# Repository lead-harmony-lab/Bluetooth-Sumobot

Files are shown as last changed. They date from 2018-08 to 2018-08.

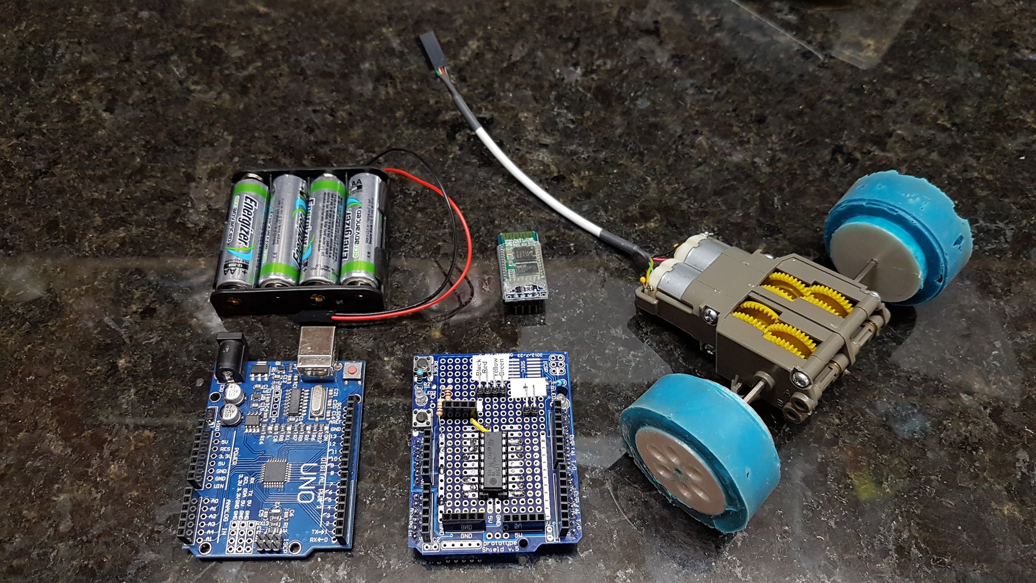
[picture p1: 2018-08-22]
20180820_223847.jpg

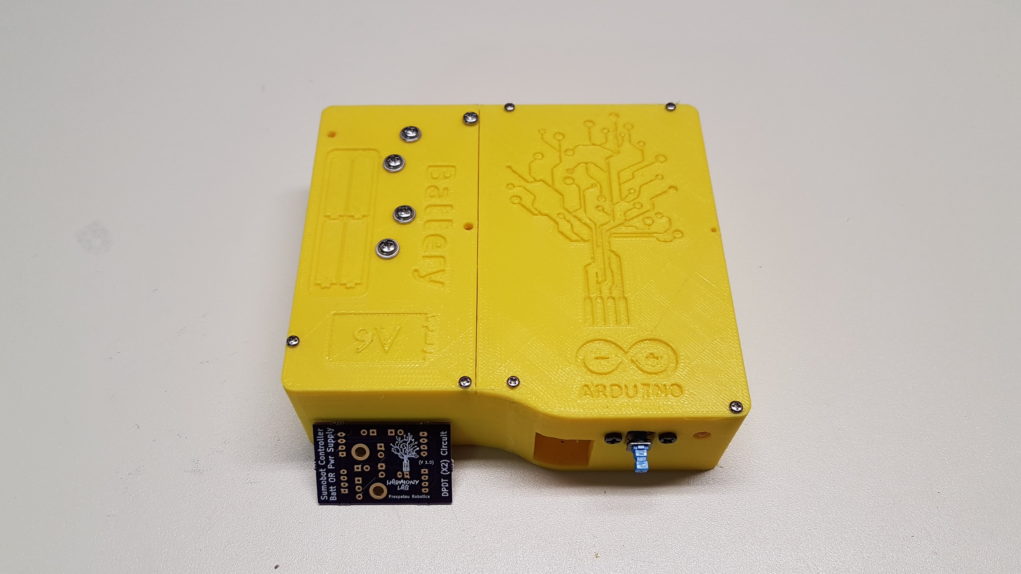
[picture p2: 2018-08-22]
20180819_121456.jpg

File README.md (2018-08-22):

# Bluetooth-Sumobot
Processing code and STL files for the BlueTooth controlled sumobot based on the HC06 module

# Controlling the Sumobot
Download and side-load the [Android app (Arduino Bluetooth Controller)](https://github.com/lead-harmony-lab/Bluetooth-Sumobot/blob/master/Arduino%20bluetooth%20controller_v1.3_apkpure.com.apk) (APK file tested in Android 8.0 on a Samsung S7) - August 2018. 
After installing the app and confirming that your BlueTooth is turned on:
1. Pair with the HC06 module (may be named HC06)
2. Enter password to pair with module (default may be '1234')
3. Launch app.
4. Select module (HC06) from the list of available devices. If not available, confirm step 1.
5. The app will ask which mode to select. Choose 'Controller mode' from top of the list.
6. Confirm solid light on the HC06 module indicating pairing was successful
7. Choose gear/settings icon from top right corner.
8. Configure the field for each icon using these strings. The icon shape is described in the [ ] braces. See [this image](https://github.com/lead-harmony-lab/Bluetooth-Sumobot/blob/master/Arduino%20bluetooth%20controller%20setup%20image.jpg) for a visual guide.
                
                [left arrow] left
                [up arrow] forward
                [right arrow] right
                [down arrow] reverse
                
                [select]
                [start]

                [square] half
                [triangle] faster
                [X] stop
                [circle] slower
REMEMBER: You must select done / checkmark on the keyboard to lock the changes into the app. Otherwise the app will continue to show 'not set' after you have entered in the appropriate text. 

9. Return to the previous screen using the Android back button.
10. Control the sumobot by pressing on the control icons.

# Customizing the Android App
The code for [a basic Android Studio project](https://github.com/lead-harmony-lab/Bluetooth-Sumobot/tree/master/Android%20Sumobot%20Controller/app/src/main) can be modified to add any additional behaviour to the controller that you require. Simply create an new 'Empty Activity' when creating a new project. When the project is loaded, copy over the basic project files into your new project's directory. **REMEMBER** to look up the MAC address of your Bluetooth module and replace the DEVICE ADDRESS in MainActivity.java in order to get this app to work with your Bluetooth module.

# Building the control board
The schematic for controlling this sumbot has been created in KiCad. The gerber files can be sent to a board house (I use [OSHPark](https://oshpark.com)) for fabrication. The schematic can also be used as a basis for putting together a breadboarded version of this project. I've included a hand-drawn image of the pinout I used for the L293D IC when connecting to the Arduino Uno.

# Model File
All of the 3D design work was done in Blender using millimeters. I used Blender 2.79b on Ubuntu 18.04 Linux.

# 3D Printing
I printed these parts out on an FDM RepRap based printer - The Robo3D R1+. Total print time is approximately 24 hours. I recommend that you print the sumobot body on its roof with the motor cavity facing up towards the nozzle. I have found that this model will print successfully without the need to also add support material. I use Matter Control software to control the 3D Printer.

# Arduino Processing Program
Code for this project is complied from a variety of sources from around the Internet. A big shout-out to all the generous people out there that share their code and who make tutorials for other people to follow. I used the Arduino IDE 1.8.5.

# Parts
* Sumobot
  * Tamiya Twin-Motor Gearbox 70097
  * 4-strand data cable
  * Silicon (OooGoo) wheel grips (you will have to design your own hubs)
* BlueTooth Module
  * HC06 Bluetooth Module https://www.ebay.ca/itm/201415076859
  * Single battery (pos & neg) terminals: https://www.ebay.ca/itm/311070764299
  * Battery conversion spring: https://www.ebay.ca/itm/172440758009
  * Latching DPDT switch: https://www.ebay.ca/itm/322498646783
  * Single-row male header pins: https://www.ebay.ca/itm/181918556293
  * Single-row female header socket: https://www.ebay.ca/itm/192600775159
  * 1K axial resistor
  * 2K axial resistor
  * 150R axial resistor
  * 100uf electrolytic capacitor: https://www.ebay.ca/itm/291535579746
  * 0.1uf ceramic capacitor: https://www.ebay.ca/itm/323377133385
  * L293D IC (Quadruple H-Bridge driver with internal fly-back diodes): https://www.ebay.ca/itm/311173671055
  * 16 pin DIP socket: https://www.ebay.ca/itm/311563518356
  * Arduino UNO: https://www.ebay.ca/itm/263452480977
  * Arduino UNO prototype shield: https://www.ebay.ca/itm/172536470483
  * 4 AA Batteries
  * 9V Battery
  * 9 Volt Battery Clip: https://www.ebay.ca/itm/263766384151
  * Hook-up wire: https://www.ebay.ca/itm/372234345012
  * Heat Shrink Tubing: https://www.ebay.ca/itm/381381208587
  * Dupont 4-Pin 2.54mm Housing: https://www.ebay.ca/itm/152837501538
  * Dupont 2-Pin 2.54mm Housing: https://www.ebay.ca/itm/331824268796
  * Dupont Female Connector Terminal: https://www.ebay.ca/itm/141975933772
  * HT-225D Dupont Crimping Tool: https://www.ebay.ca/itm/263766640490
  * M2 x 8mm self-tapping screws: https://www.ebay.ca/itm/182309825046?var=484855861567
  * M3 x 6mm self-tapping screws: https://www.ebay.ca/itm/182309825046?var=484855861608

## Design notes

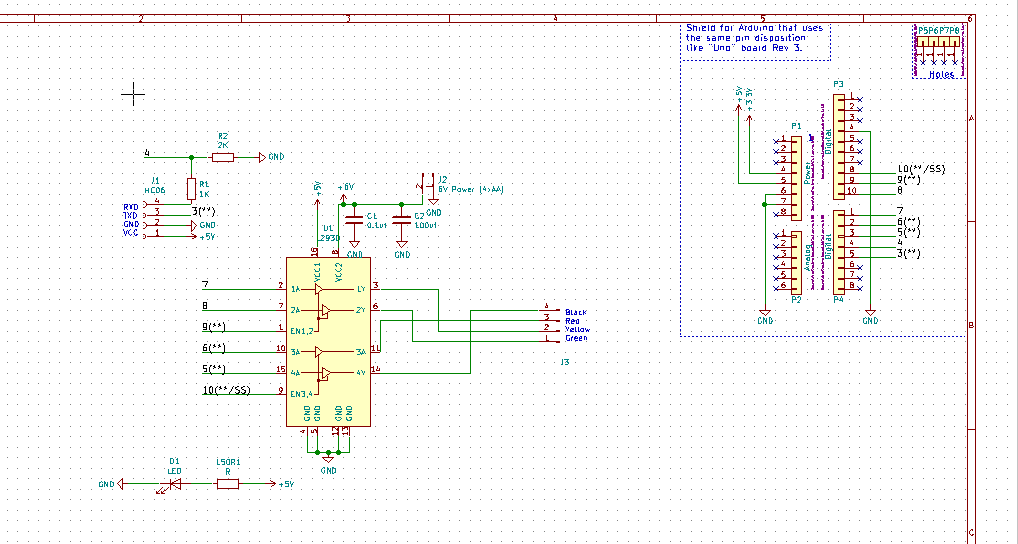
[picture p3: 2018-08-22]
Schematic.png

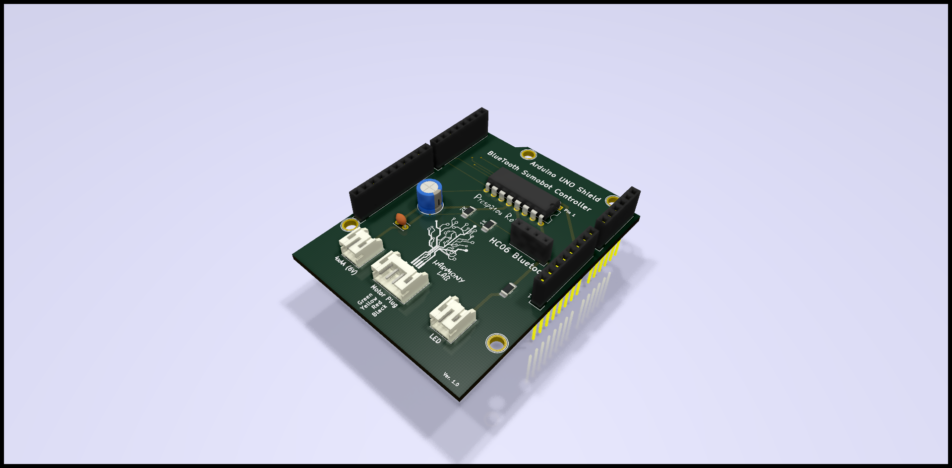
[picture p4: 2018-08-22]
L293D BlueTooth UNO Shield/Bluetooth Sumobot UNO Shield V1 Profile.png

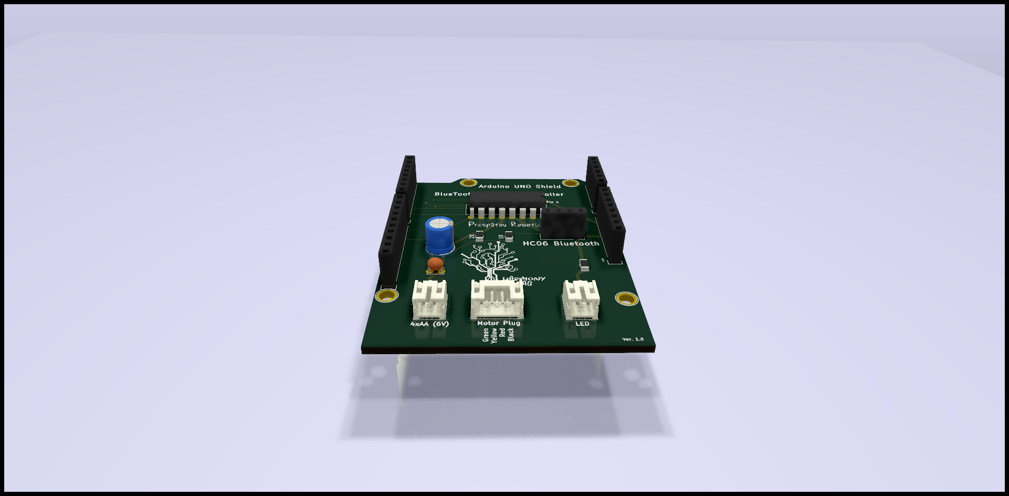
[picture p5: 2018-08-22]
L293D BlueTooth UNO Shield/Bluetooth Sumobot UNO Shield V1 Front.png

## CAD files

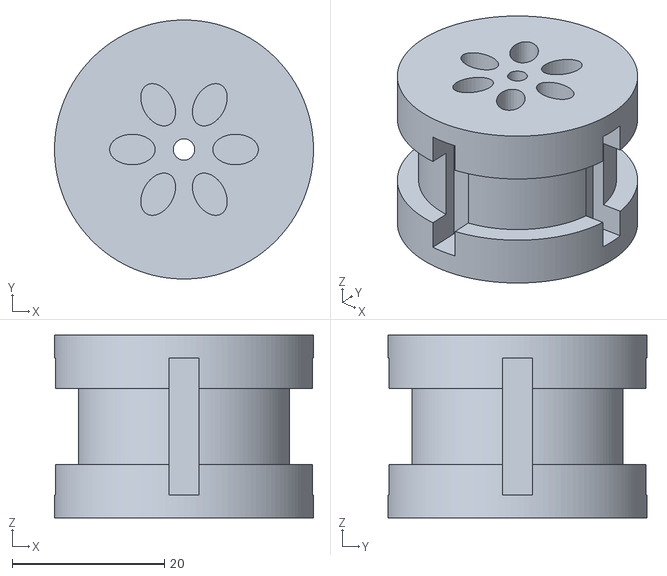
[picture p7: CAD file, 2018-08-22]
3D Model (Blender & STL)/Wheel Hub.stl
34.0 x 34.0 x 24.0

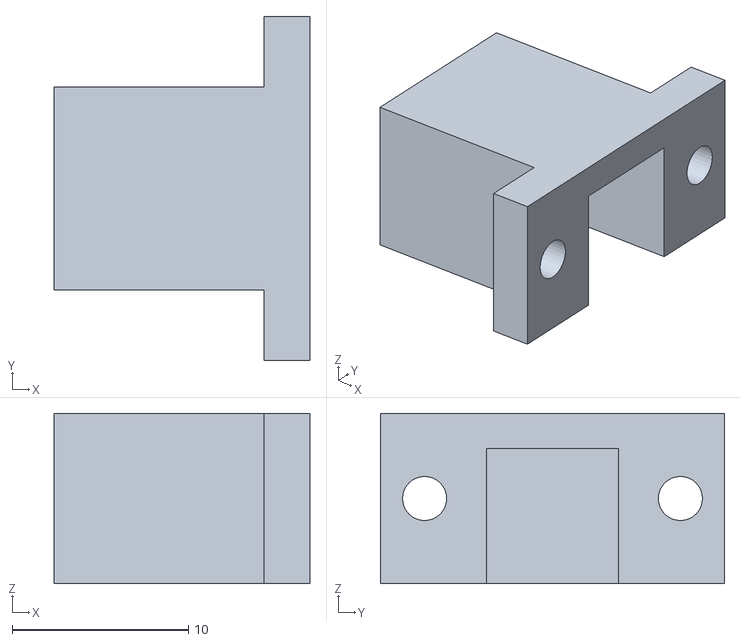
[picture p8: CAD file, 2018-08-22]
3D Model (Blender & STL)/Switch Mount.stl
14.5 x 19.5 x 9.65

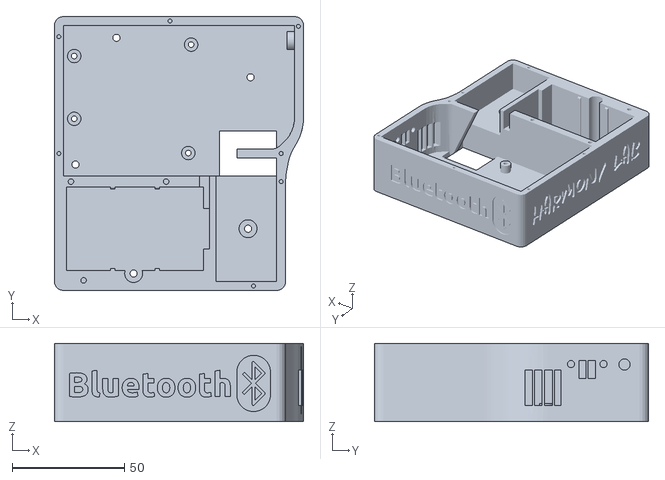
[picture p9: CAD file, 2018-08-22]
3D Model (Blender & STL)/Project Box.stl
111.0 x 122.0 x 34.9

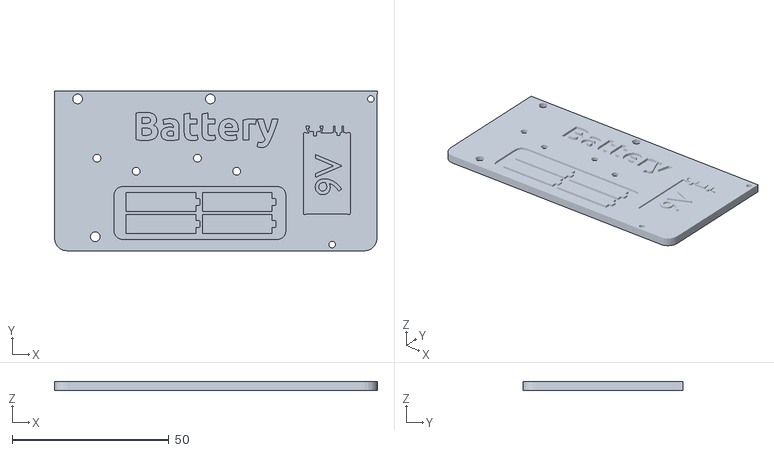
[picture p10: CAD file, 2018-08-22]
3D Model (Blender & STL)/Lid 2.stl
103.1 x 51.0 x 3.00

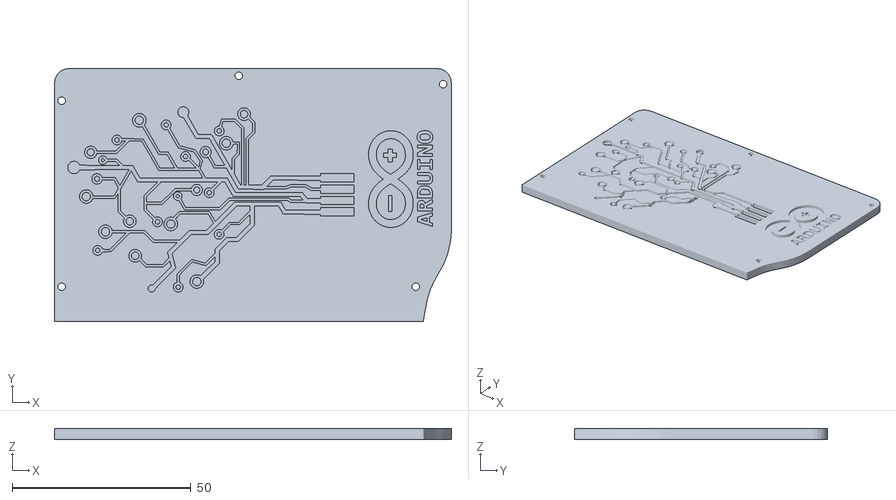
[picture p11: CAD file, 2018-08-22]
3D Model (Blender & STL)/Lid 1.stl
111.0 x 70.7 x 3.00

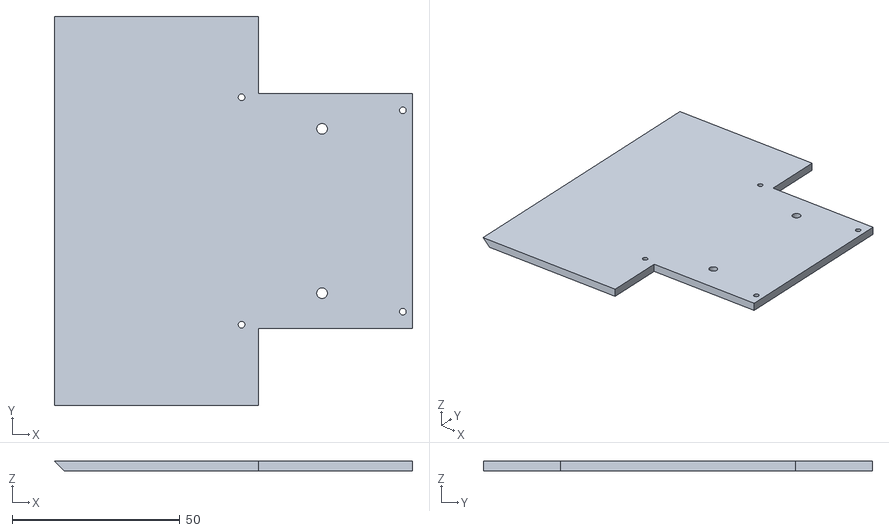
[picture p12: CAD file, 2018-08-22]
3D Model (Blender & STL)/Sumobot Motor Mounting Plate.stl
106.8 x 116.0 x 3.00

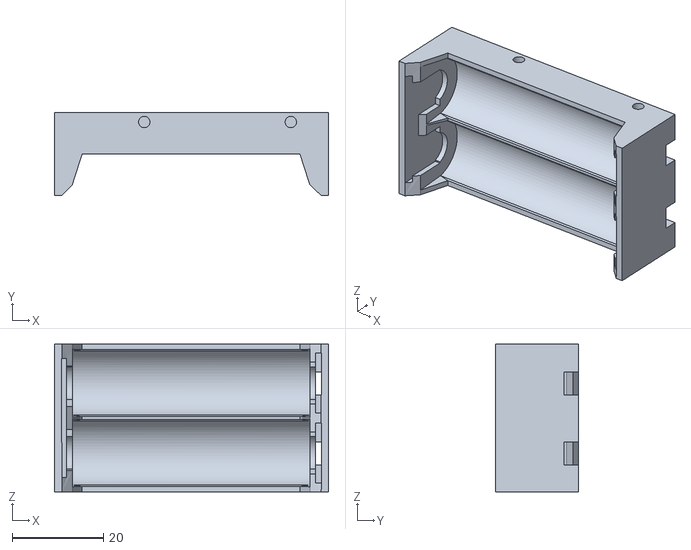
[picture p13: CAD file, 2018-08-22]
3D Model (Blender & STL)/Battery Box.stl
60.0 x 18.2 x 32.4

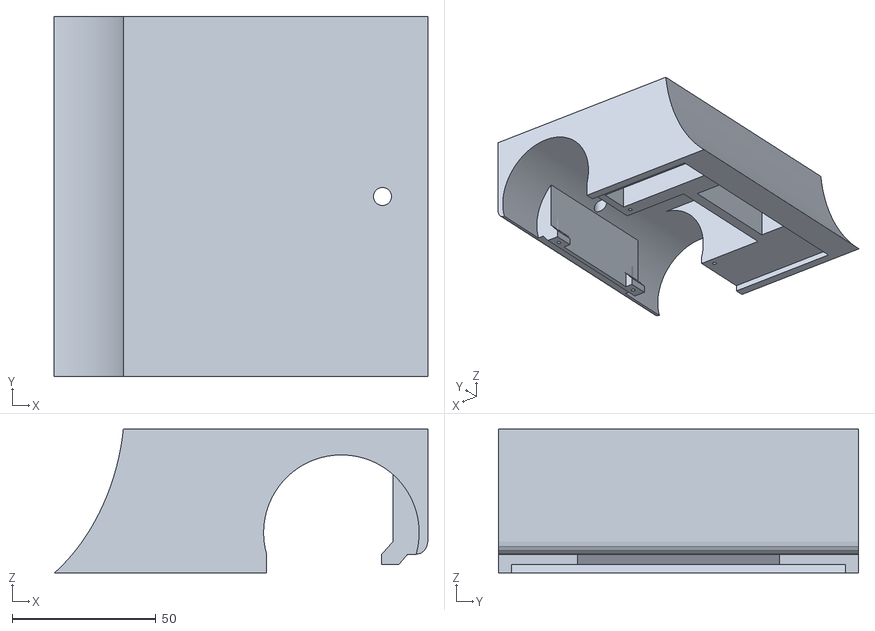
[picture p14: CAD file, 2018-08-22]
3D Model (Blender & STL)/Sumobot Body.stl
129.7 x 125.0 x 50.0

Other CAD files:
3D Model (Blender & STL)/Wheel Hub.blend

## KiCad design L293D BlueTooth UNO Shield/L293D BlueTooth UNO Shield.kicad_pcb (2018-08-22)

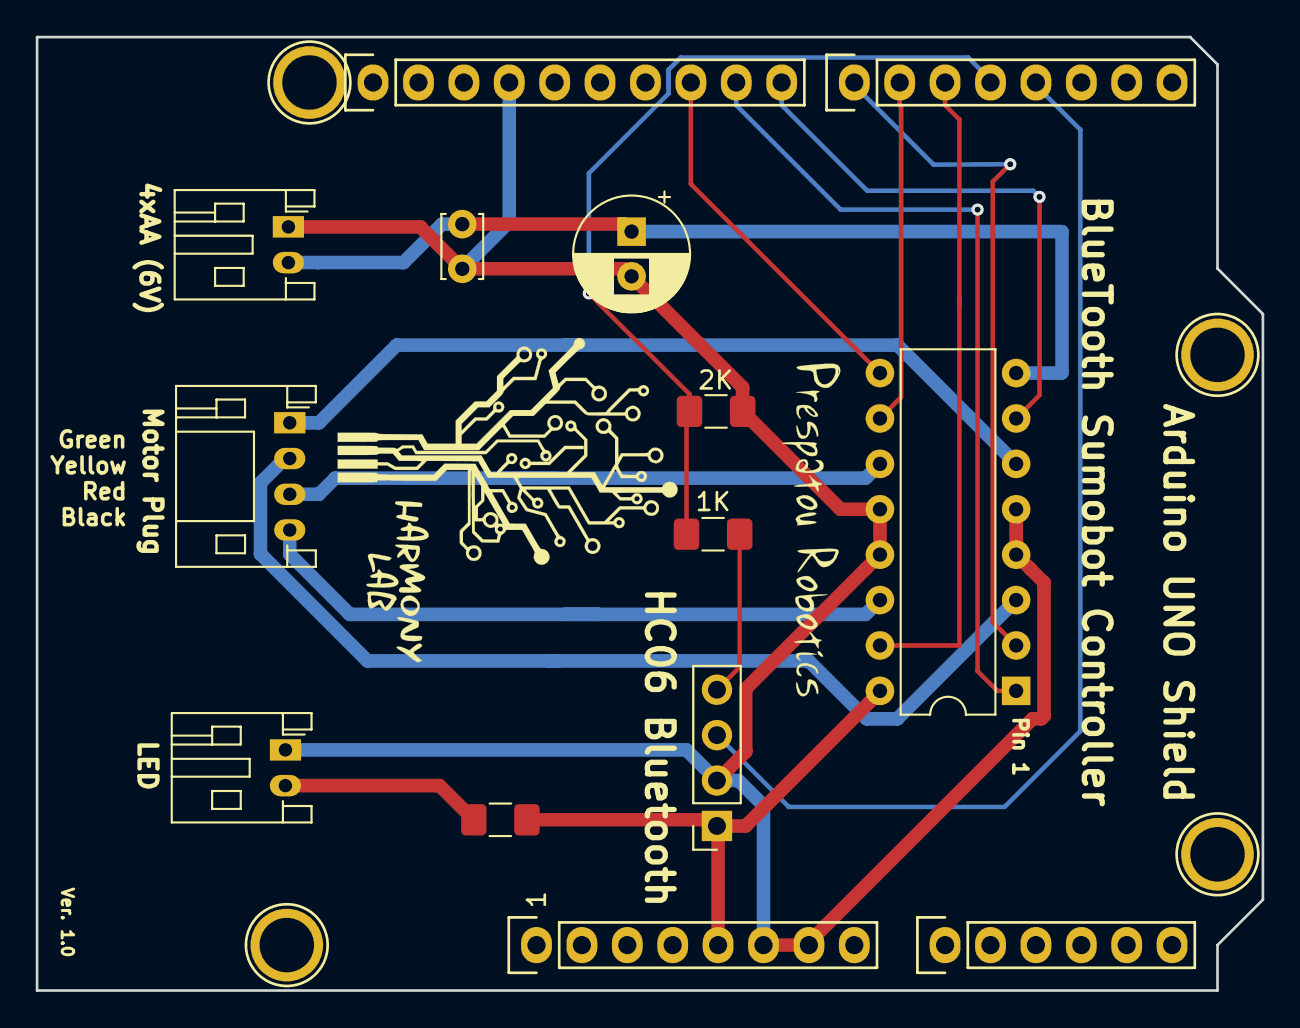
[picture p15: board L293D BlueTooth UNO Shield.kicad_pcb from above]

Board: 2 copper layers, 68.6 x 53.3 mm, 18 parts (0 on the bottom side), 17 nets.

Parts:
1K: 1K; R_1206_3216Metric_Pad1.42x1.75mm_HandSolder
2K: 2K; R_1206_3216Metric_Pad1.42x1.75mm_HandSolder
150R1: R; R_1206_3216Metric_Pad1.42x1.75mm_HandSolder
C1: 0.1uf; C_Disc_D3.4mm_W2.1mm_P2.50mm
C2: 100uf; CP_Radial_D6.3mm_P2.50mm
D1: LED; JST_PH_S2B-PH-K_1x02_P2.00mm_Horizontal
J1: HC06; PinSocket_1x04_P2.54mm_Vertical
J2: 6V Power (4xAA); JST_PH_S2B-PH-K_1x02_P2.00mm_Horizontal
J3: Motor Connector; JST_PH_S4B-PH-K_1x04_P2.00mm_Horizontal
P1: Power; Socket_Strip_Arduino_1x08
P2: Analog; Socket_Strip_Arduino_1x06
P3: Digital; Socket_Strip_Arduino_1x10
P4: Digital; Socket_Strip_Arduino_1x08
P5, P6, P7, P8: CONN_01X01; Arduino_1pin
U1: L293D; DIP-16_W7.62mm

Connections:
+5V: 150R1.1, J1.1, P1.5, U1.16
+6V: C1.1, C2.1, J2.2, U1.8
/3(**): J1.3, P4.5
/4: 1K.1, 2K.2, P4.4
/5(**): P4.3, U1.15
/6(**): P4.2, U1.10
/7: P4.1, U1.2
/8: P3.10, U1.7
/9(**): P3.9, U1.1
/10(**/SS): P3.8, U1.9
GND: 2K.1, C1.2, C2.2, D1.1, J1.2, J2.1, P1.6, P1.7, P3.4, U1.4, U1.5, U1.12, U1.13
unnamed: 150R1.2, D1.2
unnamed: 1K.2, J1.4
unnamed: J3.1, U1.6
unnamed: J3.2, U1.3
unnamed: J3.3, U1.11
unnamed: J3.4, U1.14

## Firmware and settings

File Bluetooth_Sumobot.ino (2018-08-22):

#include <SoftwareSerial.h>
SoftwareSerial BlueTooth(3, 4); // (RX, TX) - These are the pins on the Arduino we are using instead of the built-in RX and TX pins
// Connect the HC-06 TX to the Arduino RX on pin 3. 
// Connect the HC-06 RX to the Arduino TX on pin 4 through a voltage divider.

//L293D
//Motor A
const int motorPin1  = 5;   // Pin 14 of L293D
const int motorPin2  = 6;   // Pin 10 of L293D
//Motor B
const int motorPin3  = 8;   // Pin  7 of L293D
const int motorPin4  = 7;   // Pin  2 of L293D
//Enable Motors
const int enableLeftMotorSwitch = 9;   // Pin  1 of L293D
const int enableRightMotorSwitch = 10;  // Pin  9 of L293D

String msg;
char c;
int motorSpeed = 255; // Motor speed is an number between 0 - 255. Half speed is 153.

//This will run only one time.
void setup(){
  
  // HC-06 default serial speed is 9600
  BlueTooth.begin(9600); 
  Serial.begin(9600);

  //Motor Control - Motor A: motorPin1,motorpin2 & Motor B: motorpin3,motorpin4
  //Set pins as outputs
  pinMode(motorPin1, OUTPUT);
  pinMode(motorPin2, OUTPUT);
  pinMode(motorPin3, OUTPUT);
  pinMode(motorPin4, OUTPUT);

  pinMode(enableLeftMotorSwitch, OUTPUT);
  pinMode(enableRightMotorSwitch, OUTPUT);

}


void loop(){
  msg = "";

  analogWrite(enableLeftMotorSwitch, motorSpeed);
  analogWrite(enableRightMotorSwitch, motorSpeed);
  
  while(BlueTooth.available()){
    c = BlueTooth.read();
    msg += String(c);
    delay(5);
  }

  if(msg == "forward"){
    rightMotorForward();
    leftMotorForward();
  }
  else if(msg == "reverse"){
    rightMotorReverse();
    leftMotorReverse();
  }
  else if(msg == "right"){
    rightMotorStop();
    leftMotorForward();
  }
  else if(msg == "left"){
    rightMotorForward();
    leftMotorStop();
  }
  else if(msg == "half"){
    halfSpeed();
  }
  else if(msg == "stop"){
    stoprobot();
  }
  else if(msg == "faster"){
    increaseSpeed();
  }
  else if(msg == "slower"){
    decreaseSpeed();
  }

}  

// Control direction of RIGHT motor
void rightMotorForward(){
    digitalWrite(motorPin1, LOW);
    digitalWrite(motorPin2, HIGH);  
}

void rightMotorReverse(){
    digitalWrite(motorPin1, HIGH);
    digitalWrite(motorPin2, LOW);  
}

void rightMotorStop(){
    digitalWrite(motorPin1, LOW);
    digitalWrite(motorPin2, LOW);  
}

// Control direction of LEFT motor
void leftMotorForward(){
    digitalWrite(motorPin3, HIGH);
    digitalWrite(motorPin4, LOW); 
}

void leftMotorReverse(){
    digitalWrite(motorPin3, LOW);
    digitalWrite(motorPin4, HIGH); 
}

void leftMotorStop(){
    digitalWrite(motorPin3, LOW);
    digitalWrite(motorPin4, LOW); 
}


// Control BOTH motors together 
void forward()
{
    rightMotorForward();
    leftMotorForward();
}

void reverse()
{
    rightMotorReverse();
    leftMotorReverse();
}

void left()
{
    rightMotorForward();
    leftMotorReverse();
}

void right()
{
    rightMotorReverse();
    leftMotorForward();
}

void stoprobot()
{
    rightMotorStop();
    leftMotorStop();
}

void increaseSpeed()
{
  if(motorSpeed < 255)
  {
    if(motorSpeed <= 205)
    {
      motorSpeed += 50;
    }
  }
}

void decreaseSpeed()
{
  if(motorSpeed > 0)
  {
    if(motorSpeed >= 55)
    {
      motorSpeed -= 50;
    }
  }
}

void halfSpeed()
{
  motorSpeed = 155;
}

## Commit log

2018-08-22 Create LICENSE
    Attached license.
2018-08-22 Add files via upload
    Code for the Bluetooth sumobot using the HC06 module on Arduino UNO
2018-08-22 KiCad project files
    Sumobot control board schematic and KiCad files
    [L293D BlueTooth UNO Shield-B.Cu.gbl, L293D BlueTooth UNO Shield-B.Mask.gbs, L293D BlueTooth UNO Shield-B.SilkS.gbo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]
2018-08-22 Add files via upload
    3D model files of the BlueTooth sumobot
    [Battery Box.stl, Lid 1.stl, Lid 2.stl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]
2018-08-22 Update README.md
    Update BOM
2018-08-22 Update README.md
    Updates to BOM
2018-08-22 Update README.md
    Updated BOM
2018-08-22 Screenshot of configuringing BT app
    Screenshot of how to configure the Arduino BlueTooth Controller app.
2018-08-22 Add files via upload
    Added wheel hub
    [Wheel Hub.blend, Wheel Hub.stl]
2018-08-22 Android Studio code for cutom controller
    SRC folder from an Android Studio project to create a custom BlueTooth controller. Create an empty activity in Android Studio and copy the contents of the src folder into the project directory. REMEM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
2018-08-22 Add files via upload
    Board Renderings
